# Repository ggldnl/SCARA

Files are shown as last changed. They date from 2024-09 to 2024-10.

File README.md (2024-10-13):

# SCARA

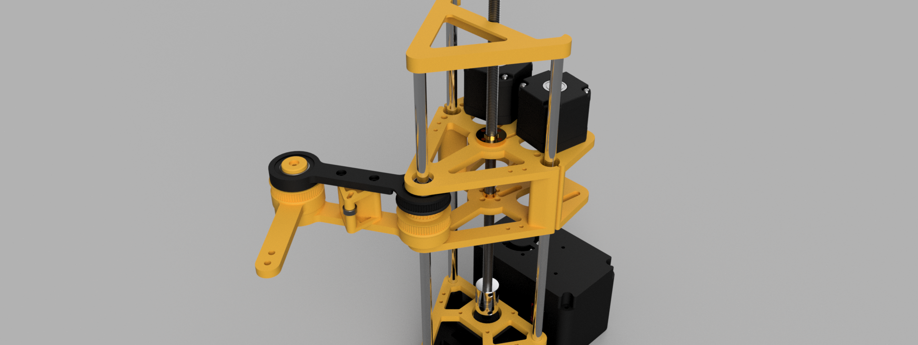
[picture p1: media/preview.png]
Preview


The SCARA (Selective Compliance Assembly Robot Arm) is a type of robotic arm designed for tasks requiring high precision and speed, like assembly and pick-and-place operations. Its configuration allows for rigid vertical movement while maintaining flexibility in the horizontal plane. 

This repository contains the design files, source code, and documentation for my SCARA robotic arm (forgive the redundancy). The arm is mostly 3d printed in order to offer a balance between affordability and functionality.

## Project history and current state

I wanted to build a simple robotic arm and found out the [pyBot](https://jjrobots.com/) project that seemed to have a lot of potential and looked like a good starting point for further development. As I finished assembling the hardware according to the guide, the domain for the website hosting the project expired and was not renewed. At the time of writing this README, the site is still offline, meaning I no longer had access to the original code. The printable files are still available on Thingiverse [here](https://www.thingiverse.com/thing:4579405), and the Hackaday page is still accessible [here](https://hackaday.io/project/175419-pybot-scara-robotic-arm-3d-printed-python).

Considering the situation, I decided to build my own robotic arm taking inspiration from this project. I redesigned everything from scratch in Fusion 360 to have precise control over the robot arm's parameters and to have accurate measurements for the inverse kinematics. The improvements with respect to the previous version include:

- tensioners for joint 2 and 3.
- endstops for each motor, essential for calibration and to recover from missed steps.
- heat set inserts to avoid screwing directly into the plastic.
- simplified assembly for joints 2 and 3.
- properly designed transmission gears.
- improved `z_base` support to joints 2 and 3, now consisting of two pieces.
- control box for better organization, with optional fan to keep the stepper driver cool.
- universal tool mounting point (not limited to the previous servo motor insert).
- clean code with no external dependency (I wrote all the libraries I used), modular and easy to read and understand .

Some renders of the arm in Fusion 360:

<table>
  <tr>
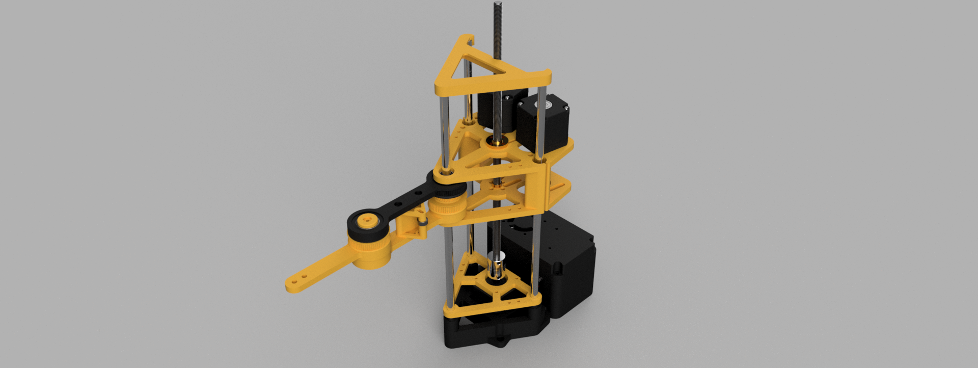
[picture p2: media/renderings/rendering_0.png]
Rendering 0
    <td></td>
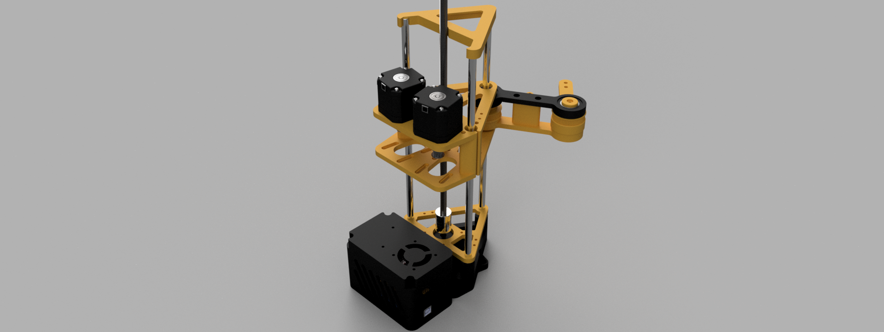
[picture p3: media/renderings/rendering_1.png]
Rendering 1
    <td></td>
  </tr>
  <tr>
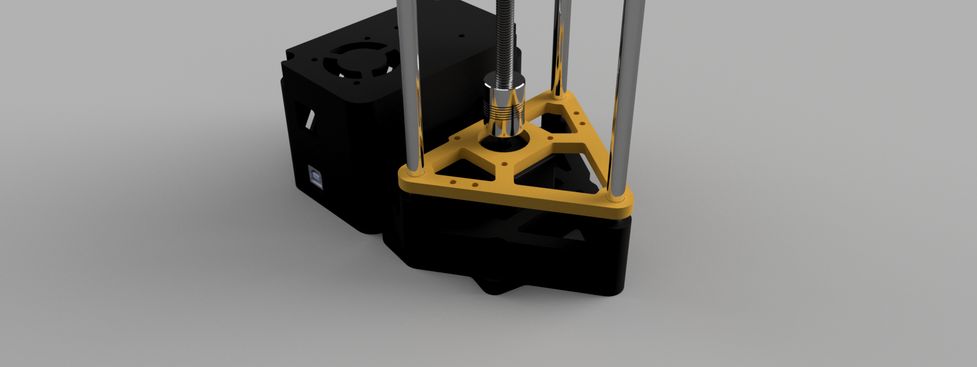
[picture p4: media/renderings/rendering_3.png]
Rendering 2
    <td></td>
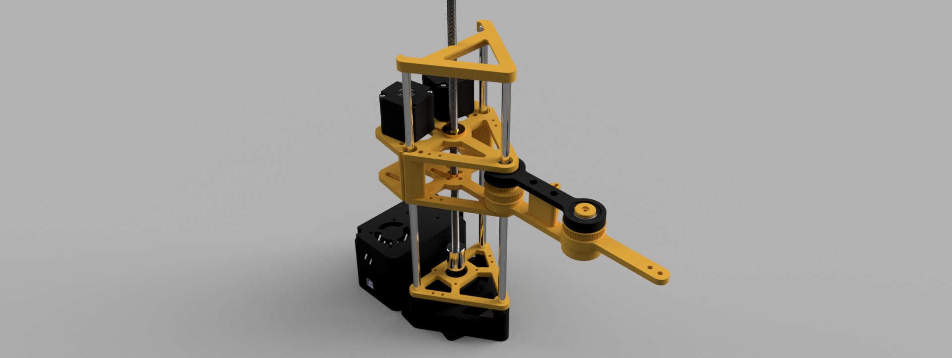
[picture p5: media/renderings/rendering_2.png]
Rendering 3
    <td></td>
  </tr>
  <tr>
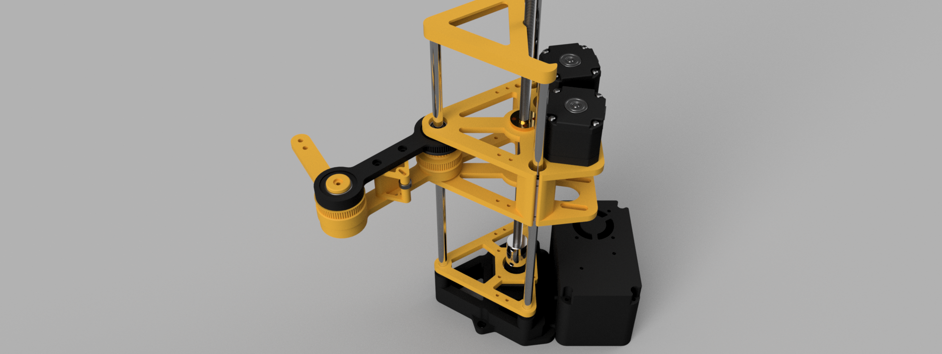
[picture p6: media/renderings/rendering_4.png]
Rendering 4
    <td></td>
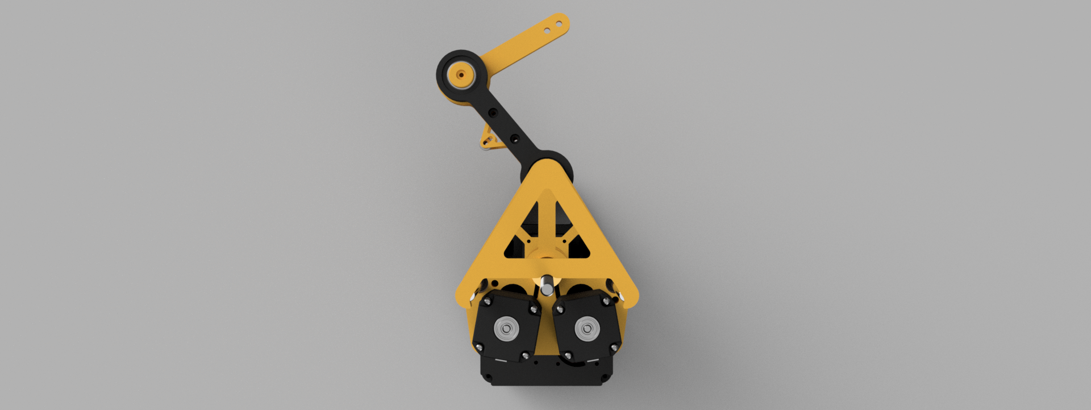
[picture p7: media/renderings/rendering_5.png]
Rendering 5
    <td></td>
  </tr>
</table>

The original project used a DEVIA board, which is an Arduino Zero with built-in sockets for three A4988 stepper motor drivers and onboard drivers for four servos. I opted for an Arduino Uno paired with a CNC shield because it is more accessible, easy to find, and I happened to have both lying around. This setup provides four sockets for stepper drivers and three pins that can be used for the endstops or the end-effector. I also added a 12V mini fan (used for 3d printers) to cool the stepper drivers but this is totally optional. 

## Examples

Homing (https://www.youtube.com/watch?v=YOUTUBE_VIDEO_ID_HERE)

Morning routine (https://www.youtube.com/watch?v=YOUTUBE_VIDEO_ID_HERE)

Pen plotter (https://www.youtube.com/watch?v=YOUTUBE_VIDEO_ID_HERE)

Following a simple straight line (https://www.youtube.com/watch?v=YOUTUBE_VIDEO_ID_HERE)

## 3D printing

You can find all the parts to print in the [hardware/printed_parts](/hardware/printed_parts) folder. Alternatively, you can get them on the platforms below: 

<p align="center">
  <a href="https://makerworld.com/en/models/572256#profileId-492414">
    Open on Makerworld
  </a>
</p>

<p align="center">
  <a href="https://www.thingiverse.com/thing:6743905">
    Open on Thingiverse
  </a>
</p>

<p align="center">
  <a href="https://www.printables.com/en">
    Open on Printables
  </a>
</p>

## Assembly instructions

Check out [here](/hardware/BOM.md) for the Bill of Materials and some notes on what you will need. [Here](/hardware/ASSEMBLY.md) you can find the pdf version of the assembly instructions (that also contains a section on the electronics).

Use [this QR code](https://instructions.online/?id=12092-scara) if you want to follow the instructions on another device:

<p align="center">
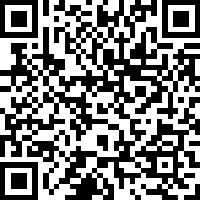
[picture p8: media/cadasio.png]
  
</p>

<!--
<p align="center">
  <a href="https://instructions.online/?id=12092-scara">
    <img src="https://gist.githubusercontent.com/ggldnl/0cb170e629d8188959e9c26c36bc32bd/raw/button_assembly-instructions_fixed_w300_h50.png" alt="Assembly instructions"/>
  </a>
</p>
-->

<!--
## Electronics

<p align="center">
  <img src="media/electronics_stepper_motors.png"/>
</p>

Note:
- Sometimes the cables can have a different color order at the extrema; you should match the connections in this picture;
- Use 3 jumpers for each stepper driver to set the microstepping to 16 (this is what is currently in the config)
  or change the `MICROSTEPPING` value in the config;

<p align="center">
    <img src="media/electronics_limit_switches.png"/>
</p>

After assembling everything and putting together the electronics: download the project > open `software/SCARA/SCARA.ino` from the arduino IDE > compile and upload to the arduino.

-->

## Brief software overview

Summary of the content of each file:

- `vector.hpp`: variable-length vector template class;
- `matrix.hpp`: matrix template class; each matrix has fixed size (not resizable) and exposes methods to compute the determinant, transpose, inverse and even the pseudoinverse along with the classic utility methods   (e.g. indexing, multiplication by matrix/vector etc.);
- `structs.hpp`: structures used to make the code more readable and compact (Point, IKSolution, Steps);
- `button.hpp`: code to handle button events (button pressed and released);
- `logger.hpp`: logger to print formatted strings filtering by logging level (info, warn, error, debug);
- `stepper.hpp`: code to control a stepper motor and make it cover a distance following a trapezoidal/triangular/linear speed profile (everything is expressed in steps, steps/s, steps/s^2);
- `config.hpp`: config file with kinematic structure and velocity/acceleration related constants; You can edit this to adapt the code to your needs;
- `kinematics.hpp`: everything related to this particular robot's kinematics (direct and inverse kinematics, joint velocities computation, ...);
- `SCARA.ino`: main sketch exposing methods to follow a specified trajectory and reach a cartesian point or a joint configuration;

We can use:
- `reachJoint(IKSolution, ...)` to reach a joint configuration with a trapezoidal speed profile;
- `reachCartesian(Point, ...)` to reach a cartesian point with a trapezoidal speed profile;
- `moveStraightLine(Point, Point, ...)` to move between two cartesian points in a straight line interpolating on intermediate positions; we use a linear speed profile between each pair of intermediate points;
- `moveArc(Point, Point, ...)` to move between two cartesian points on an arc interpolating on intermediate positions; we use a linear speed profile between each pair of intermediate points;
- `executeTrajectory(Vector<Point>, ...)` to follow geometric paths; we use the `moveArc(Point, Point, ...)` method between each pair of points; 

<!--
A trajectory is a geometric path + a timing law. In our case things are much simpler and a trajectory is assumed to be a list of points to be reached one after another with a certain velocity (in steps/s). Even if the code to compute joint velocities and thus realize a particular end effector velocity is partially there, I'm not using it (yet?). 

To define your trajectory, replace the section in `SCARA.ino` where the points are added to the trajectory vector. The points in the following example describe a circular trajectory with radius 0.05, center (0.12, 0) and z=0.05 meters:

```cpp
  // Circle (10 points) with radius 0.05  and center (0.12, 0) [meters]
  trajectory.pushBack(Point(0.17, 0.00, 0.05));
  trajectory.pushBack(Point(0.16, 0.03, 0.05));
  trajectory.pushBack(Point(0.14, 0.05, 0.05));
  trajectory.pushBack(Point(0.10, 0.05, 0.05));
  trajectory.pushBack(Point(0.08, 0.03, 0.05));
  trajectory.pushBack(Point(0.07, 0.00, 0.05));
  trajectory.pushBack(Point(0.08, -0.03, 0.05));
  trajectory.pushBack(Point(0.10, -0.05, 0.05));
  trajectory.pushBack(Point(0.14, -0.05, 0.05));
  trajectory.pushBack(Point(0.16, -0.03, 0.05));
```

Calling `executeTrajectory(trajectory)` after this will make the robot execute the trajectory (if feasible i.e. all points are within the reachable workspace and the velocities and acceleration are well conditioned). By default the velocities and acceleration used are the ones defined in the `config.cpp` file but can bypassed using the `executeTrajectory` method's parameters.

-->

## TODO

- [x] Add more renderings
- [ ] Add assembly pdf instructions
- [ ] Update Cadasio instructions
- [x] Add schematic diagram
- [x] Forget AccelStepper/MobaTools and write your own library to simultaneously control multiple steppers
- [x] Add forearm calibration endstop
- [x] Complete the BOM with the list of M3 screws needed
- [ ] Update STLs

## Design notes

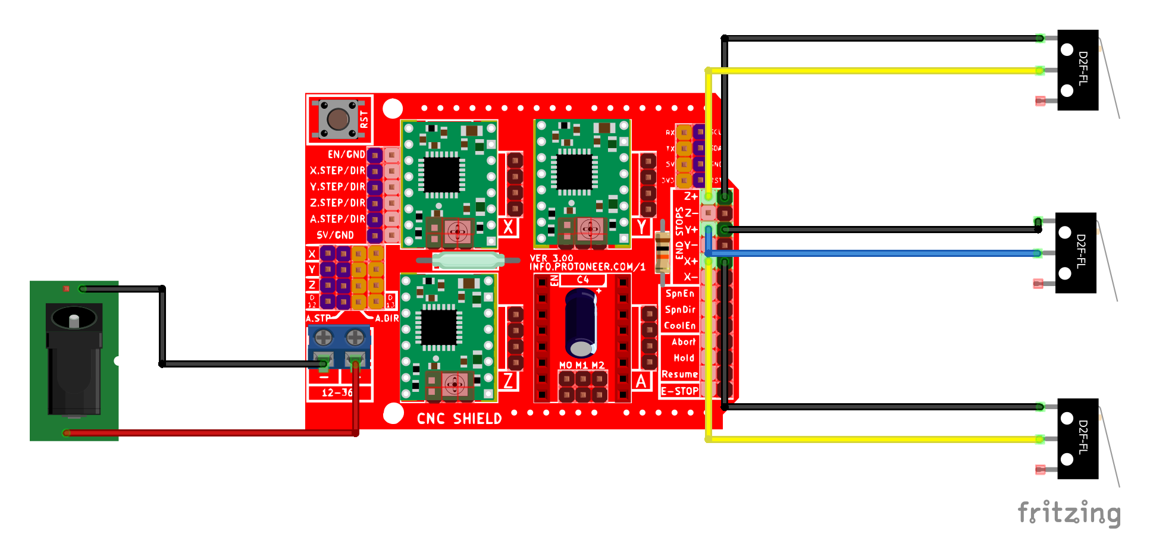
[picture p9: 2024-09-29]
media/electronics_limit_switches.png

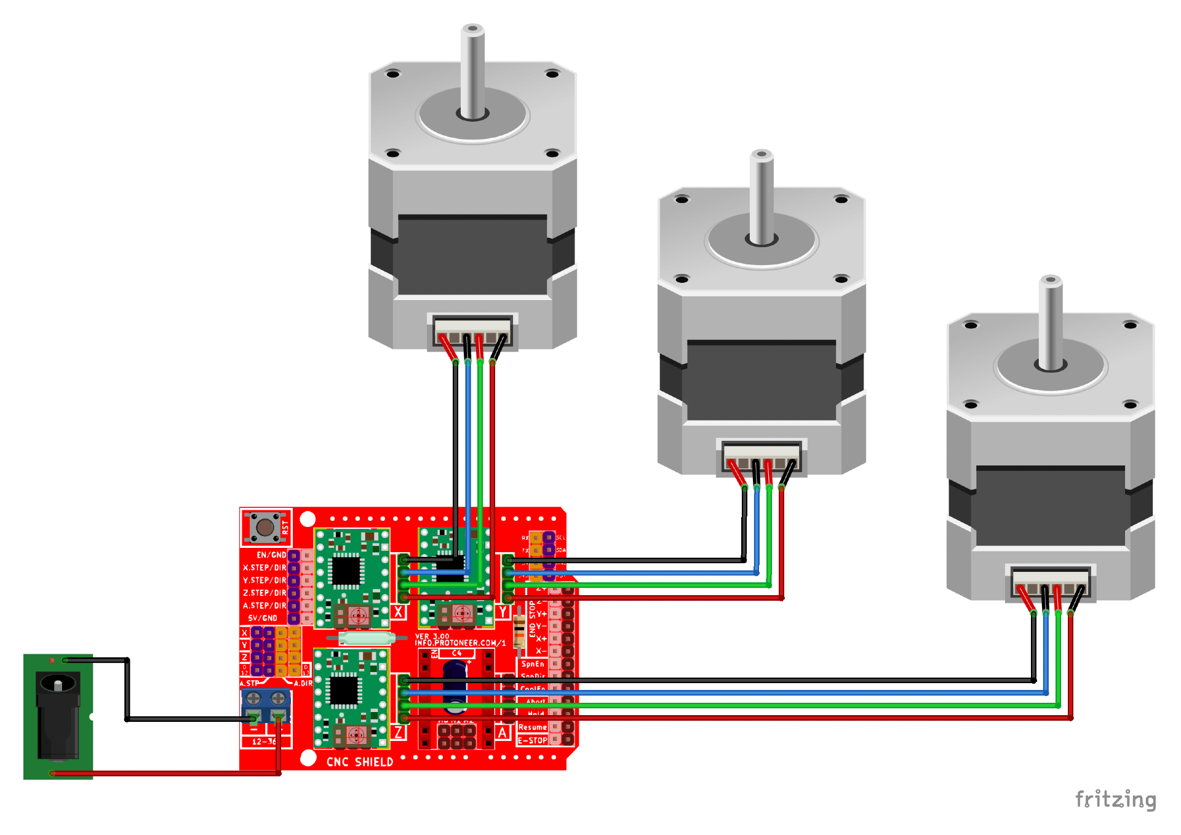
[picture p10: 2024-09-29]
media/electronics_stepper_motors.png

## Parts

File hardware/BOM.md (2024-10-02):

# Bill of Materials (BOM)

| Component | Quantity | Description | Cost (per unit) |
|---|---|---|---|
| NEMA17 stepper motor  | 3 | 1.8° step angle, 12V, 1.5A | € 8.88 |
| Arduino Uno | 1 | | €22.99 |
| CNC shield | 1 | Arduino Uno shield for CNCs | €16.79 |
| Stepper motor driver  | 3 | Stepper drivers based on A4988 | € 1.79 |
| Timing belt | 3 | GT2, 6mm width, 280mm long | € 1.92 |
| Lead screw | 1 | 8mm diameter, 300mm length, with POM nut | € 5.50 |
| Aluminum rods | 3 | 8mm diameter, 300mm length | € 9.99 |
| Pulley | 3 | GT2 for 6mm belt, 16 teeth, 5mm bore | € 1.36 |
| Coupler | 1 | 5mm to 8mm coupler | € 1.60 |
| LM8LUU linear bearing | 3 | Linear bearing, 8mm x 15mm x 45mm | € 2.40 |
| 6002-2RS | 3 | Ball bearing, 15mm x 32mm x 9mm | € 1.42 |
| M3 hex screw kit | 1 | See notes | €11.99 |
| M2 hex screw kit | 1 | See notes | € 7.99 |
| Heat set inserts | 1 | See notes | € 0.06 |
| Locknuts | 1 | See notes | € 0.06 |
| Micro switches | 3 | | € 0.22 |

Total: 150.8 (omitting heat set inserts and locknuts)

## Notes

- Keep in mind that the cost per unit, and consequently the total cost, may vary depending on where you source the parts. For this reason I have not included sourcing links. The listed unit prices reflect now much I paid for each item.
- I did not include zip ties, spiral wraps for the cables and the labels (for which you will also need a labeling machine).
- The aluminum rods I bought are hollow, but this doesn't matter. It's just what was available at the time.
- I added a 12V fan to cool down the stepper drivers but this is totally optional and thus omitted from the BOM. The fan was too loud so I also added a step down converter to decrease the voltage, also optional. If you don't have a step down laying around you can also:
    1. use the fan connecting it directly to the power jack if it's 12V;
    2. use a variable resistor to create a voltage divider and lower its input voltage; this is kind of sketchy and the resistor can get very hot, not recommended;
    3. use a 5V fan and connect it to the 5V and GND pins of the CNC shield;
    
    I provided 3 versions of the control box lid to accomodate each case.
- Number of locknuts used (only where vibrations would unscrew a regular nut): 8
- Number of heat set inserts used: 24
- Complete list of M2 screws and nuts used: 6x M2x16 screw + 6x M2 nuts to keep the micro switches in place 
- Complete list of M3 screws and nuts used:
        2x M3x35
        3x M3x10 (control box lid)
        2x M3x10 (mount arduino to control box)
        2x M3x10 (join control box to base)
        5x M3x10 (forearm)
        10x M3x8 (two z_base and lead screw nut assembly)
        6x M3x16 (limit switches) 
        8x M3 locknuts (limit switches and bottom of the forearm)
        optional - 4x M3x18 (mount fan)
        optional - 2x M3x16 (mount step down voltage regulator)

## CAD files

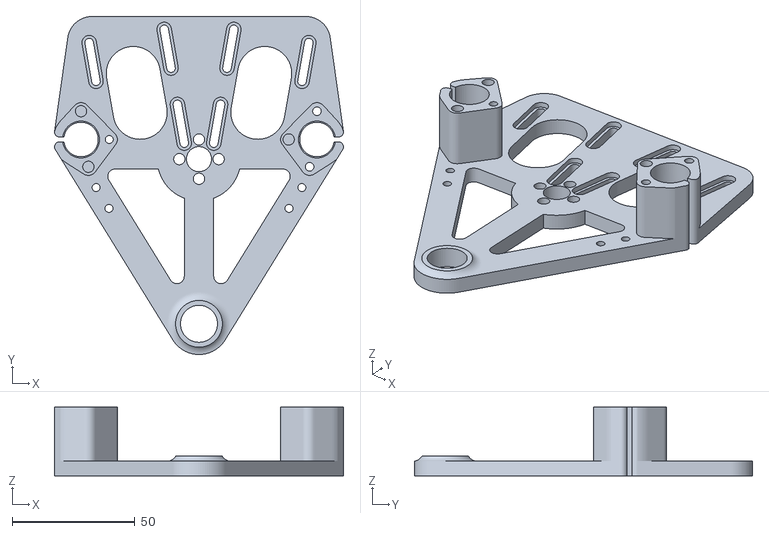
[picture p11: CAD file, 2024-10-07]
hardware/printed_parts/z_base.stl
117.6 x 137.5 x 28.0

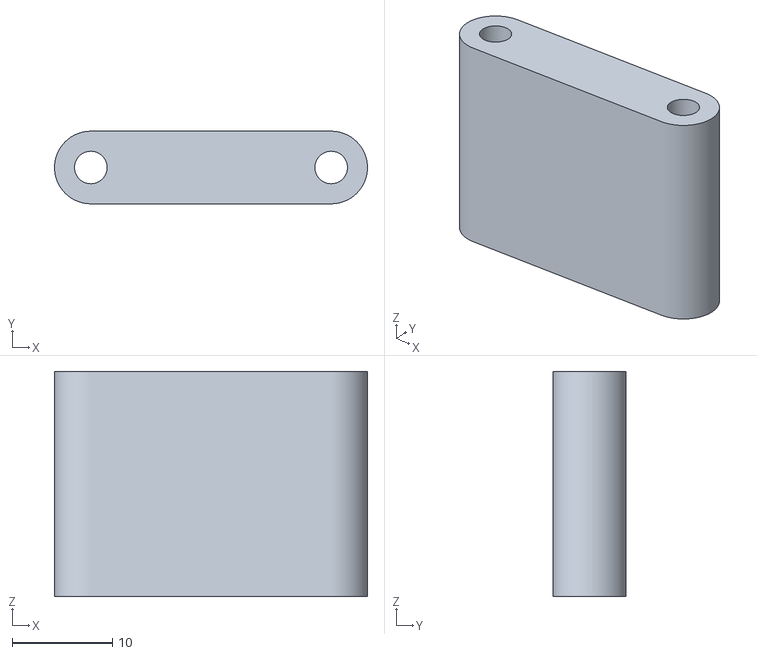
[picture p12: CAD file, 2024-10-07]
hardware/printed_parts/tensioner_bridge.stl
31.2 x 7.25 x 22.5

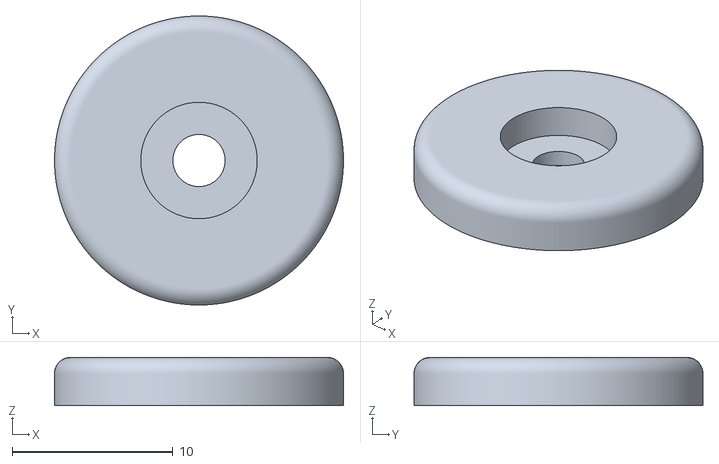
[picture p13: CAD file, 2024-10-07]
hardware/printed_parts/cap.stl
18.0 x 18.0 x 3.00

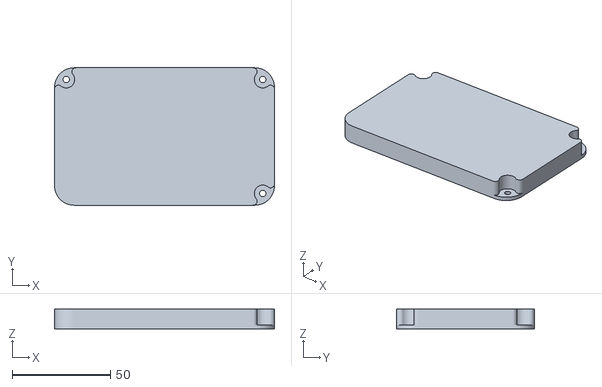
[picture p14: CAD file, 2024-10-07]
hardware/printed_parts/lid.stl
112.0 x 70.0 x 10.0

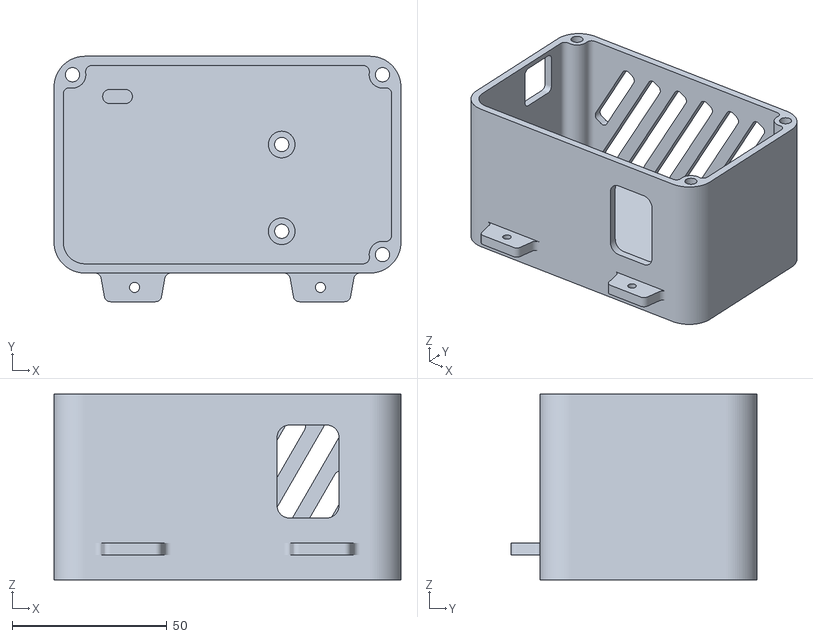
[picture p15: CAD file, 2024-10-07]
hardware/printed_parts/control_box.stl
112.0 x 79.2 x 60.0

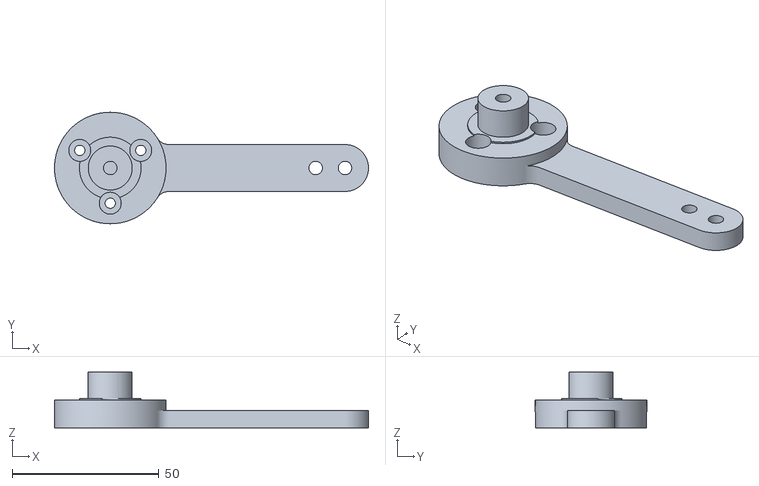
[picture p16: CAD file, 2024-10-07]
hardware/printed_parts/forearm.stl
107.0 x 38.0 x 19.0

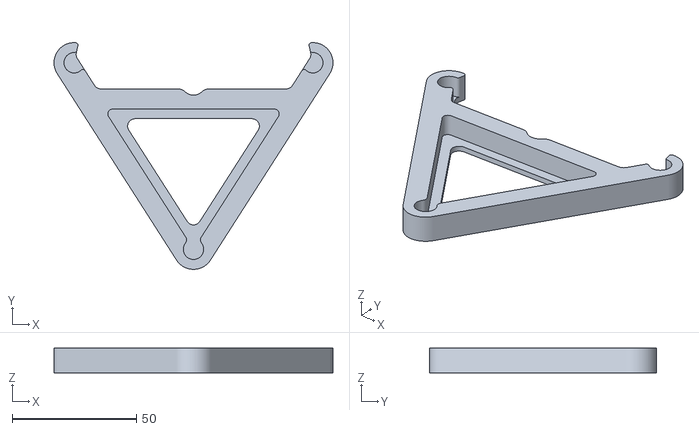
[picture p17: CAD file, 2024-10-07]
hardware/printed_parts/top_triangle.stl
112.2 x 91.2 x 10.0

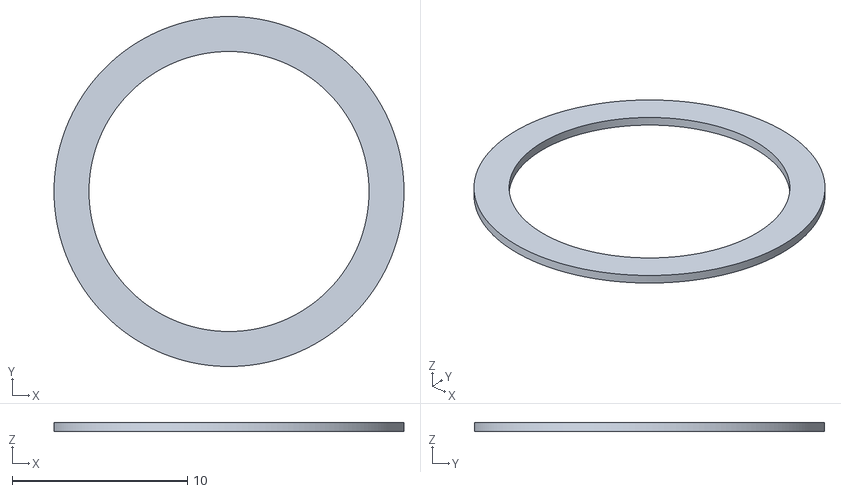
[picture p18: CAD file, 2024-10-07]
hardware/printed_parts/spacer_bottom.stl
20.0 x 20.0 x 0.5

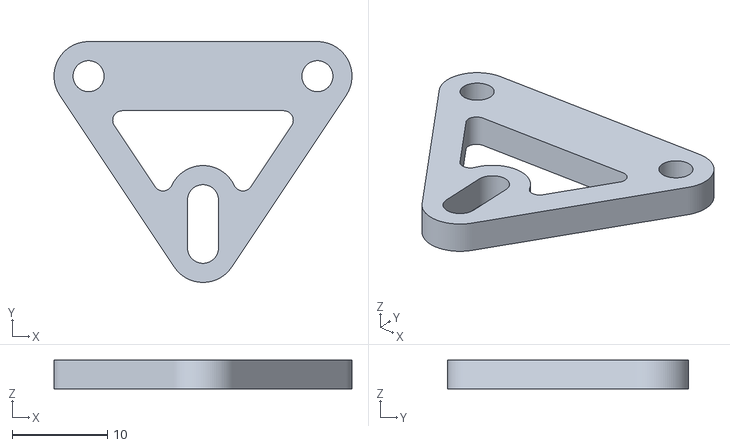
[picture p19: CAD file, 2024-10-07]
hardware/printed_parts/tensioner.stl
31.2 x 25.2 x 3.00

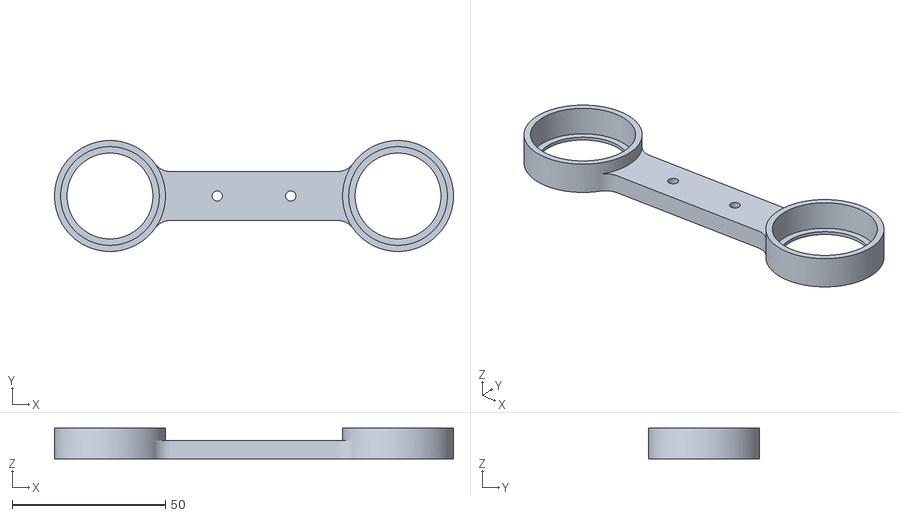
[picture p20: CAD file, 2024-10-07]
hardware/printed_parts/arm_bottom.stl
130.2 x 36.2 x 10.0

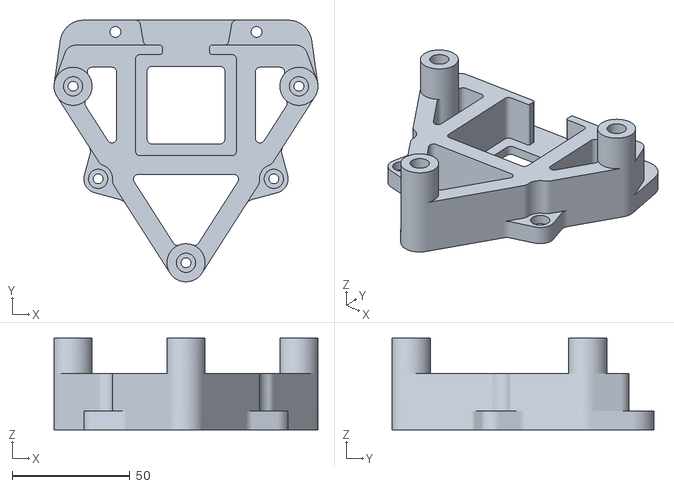
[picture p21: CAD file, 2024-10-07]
hardware/printed_parts/base.stl
112.2 x 111.2 x 39.0

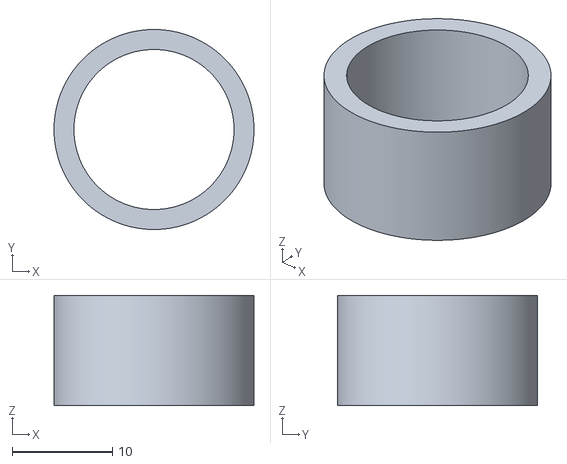
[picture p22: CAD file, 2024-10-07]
hardware/printed_parts/spacer_top.stl
20.0 x 20.0 x 11.0

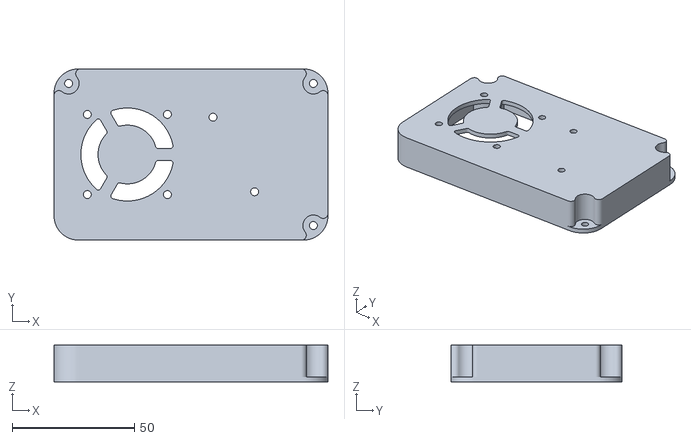
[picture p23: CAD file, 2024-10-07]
hardware/printed_parts/lid_fan_step_down.stl
112.0 x 70.0 x 15.0

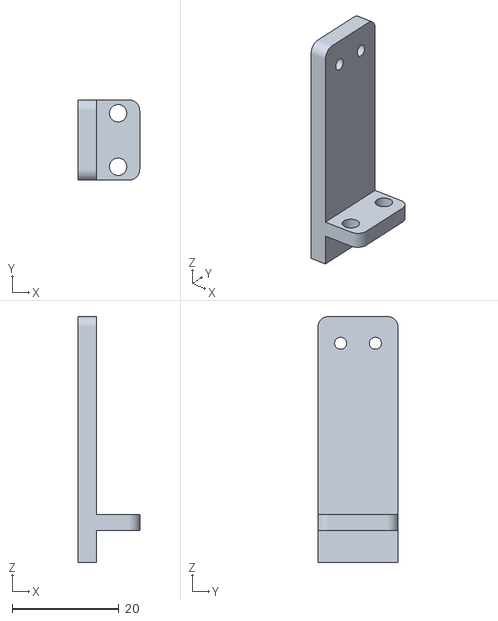
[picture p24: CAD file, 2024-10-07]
hardware/printed_parts/z_endstop.stl
11.5 x 15.0 x 46.0

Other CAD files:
hardware/printed_parts/bottom_triangle.stl
hardware/printed_parts/lid_fan.stl
hardware/printed_parts/arm_top.stl
hardware/printed_parts/xy_endstop.stl
hardware/printed_parts/forearm_reduction.stl
hardware/printed_parts/tensioner_spacer_bottom.stl
hardware/printed_parts/tensioner_spacer_top.stl
hardware/printed_parts/z_base_arm_offset.stl

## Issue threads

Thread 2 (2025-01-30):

The inverse kinematics solution doesn't seem to work

mikhailshevtsov, 2025-01-30:

ggldnl, 2025-01-30:
Can you provide more on the issue?

ggldnl, 2025-01-30:
I already accounted for the fact that link 2 and link 3 are not independent in the code, have you tried it?
The dependence is purely mechanical, due to the motors positioning and transmissions. If you just consider the kinematic model there is no dependence. This is the reason why I momentarily stopped developing the arm, the code is ready and scalable but I'm planning to change almost everything hardware-wise.

Since the two links should be independent the coupling does not show up in the kinematic formulas (in `kinematics.hpp`), but in the main file (`SCARA.ino`, specifically at lines 344-347), when converting from joint values to steps, you can see the offset is added.

Closed 2025-01-31.

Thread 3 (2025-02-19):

SCARA.ino line 347

mikhailshevtsov, 2025-02-19:
Can you explain why we need to adjust third joint by a factor of 2? How to calculate that factor?

ggldnl, 2025-02-19:
It was an empirical finding. After a lot of trials I found that that was pretty much the right value to account for the displacement introduced by the structure of the arm but it is for no means mathematically accurate and this was, once again, a reason why I want to redesign it completely. Let me know if you find a better way of doing this but just out of curiosity, hopefully this problem won't be present in the rework

mikhailshevtsov, 2025-02-19:
Thanks for clarification. I'm also trying to find it empirically. 1.85 seems to be the closest so far.

ggldnl, 2025-02-19:
I suggest you not to put a lot of time into it, unless you already built the arm. If you have experience with cad we can get in touch and work together on the new version

Closed 2025-02-21.

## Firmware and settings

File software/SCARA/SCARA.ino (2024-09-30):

#include "config.hpp"
#include "logger.hpp"
#include "button.hpp"
#include "vector.hpp"
#include "stepper.hpp"
#include "structs.hpp"
#include "kinematics.hpp"

// Function declarations
void executeTrajectory(Vector<Point>&, const double = MIN_VELOCITY_STEPS_S, const double = MIN_VELOCITY_STEPS_S, const double = MIN_VELOCITY_STEPS_S);
void moveStraightLine(const Point&, const Point&, const double = MIN_VELOCITY_STEPS_S, const double = MIN_VELOCITY_STEPS_S, const double =  MIN_VELOCITY_STEPS_S, const int = 20);
void moveArc(const Point&, const Point&, const Point&, const double = MIN_VELOCITY_STEPS_S, const double = MIN_VELOCITY_STEPS_S, const double =  MIN_VELOCITY_STEPS_S, const int = 20);
void reachCartesian(const Point&, const double = MIN_VELOCITY_STEPS_S, const double = MAX_VELOCITY_STEPS_S, const double = MIN_VELOCITY_STEPS_S, const double = ACCELERATION);
void reachJoint(const IKSolution&, const double = MIN_VELOCITY_STEPS_S, const double = MAX_VELOCITY_STEPS_S, const double = MIN_VELOCITY_STEPS_S, const double = ACCELERATION);
Steps IKSolution2Steps(const IKSolution&);
void homeAxis(StepperMotor&, Button&, long, double = HOMING_VELOCITY_STEPS_S);
void homeAll();
void moveAll();
void disable();
void enable();

// Define the steppers
StepperMotor stepper1(STEPPER_1_STEP_PIN, STEPPER_1_DIR_PIN);
StepperMotor stepper2(STEPPER_2_STEP_PIN, STEPPER_2_DIR_PIN);
StepperMotor stepper3(STEPPER_3_STEP_PIN, STEPPER_3_DIR_PIN);

// Define the buttons
Button button1(STEPPER_1_LIMIT_SWITCH_PIN);
Button button2(STEPPER_2_LIMIT_SWITCH_PIN);
Button button3(STEPPER_3_LIMIT_SWITCH_PIN);

// Define the trajectory to follow
Vector<Point> trajectory;

void setup() {

  delay(2000);

  // Initialize serial communication
  Serial.begin(115200);

  // Set log level to INFO
  Logger::setLogLevel(Logger::DEBUG);

  // Initialize the limit switch pins
  pinMode(STEPPER_1_LIMIT_SWITCH_PIN, INPUT_PULLUP);
  pinMode(STEPPER_2_LIMIT_SWITCH_PIN, INPUT_PULLUP);
  pinMode(STEPPER_3_LIMIT_SWITCH_PIN, INPUT_PULLUP);
  Logger::info("Set up limit switches.");

  // Enable the board
  pinMode(ENABLE, OUTPUT);
  enable();
  
  // Home axis
  homeAll();
  Logger::info("All axis homed.");

  /* --------------------------- Execute trajectory --------------------------- */

  // Define an straight line
  trajectory.pushBack(Point(0.10, -0.05, 0.05));
  trajectory.pushBack(Point(0.10, -0.04, 0.05));
  trajectory.pushBack(Point(0.10, -0.03, 0.05));
  trajectory.pushBack(Point(0.10, -0.02, 0.05));
  trajectory.pushBack(Point(0.10, -0.01, 0.05));
  trajectory.pushBack(Point(0.10, 0.01, 0.05));
  trajectory.pushBack(Point(0.10, 0.02, 0.05));
  trajectory.pushBack(Point(0.10, 0.03, 0.05));
  trajectory.pushBack(Point(0.10, 0.04, 0.05));
  trajectory.pushBack(Point(0.10, 0.05, 0.05));
  
  // Position above the first point, a little higher
  reachCartesian(Point(trajectory[0].x, trajectory[0].y, trajectory[1].z + 0.01));

  // Wait for a keypress of the first endstop to start the motion
  while (!button1.pressed()) delay(10);

  executeTrajectory(trajectory, MIN_VELOCITY_STEPS_S, 2000, MIN_VELOCITY_STEPS_S); // peak at 2000 steps/s

  delay(2000);
  disable();
}

/* ------------------------------ Trajectories ------------------------------ */

void executeTrajectory(
    Vector<Point>& trajectory, 
    const double initialVelocity,
    const double maxVelocity,
    const double finalVelocity
    ) {

    for (int i = 0; i < trajectory.getSize() - 1; ++i) {

        // Define velocities
        double vi = i == 0 ? initialVelocity : maxVelocity;
        double vf = i == trajectory.getSize() - 2 ? finalVelocity : maxVelocity;

        moveStraightLine(trajectory[i], trajectory[i + 1], vi, maxVelocity, vf);
    }
}

void moveStraightLine(
  const Point& start,
  const Point& end,
  const double initialVelocity, 
  const double maxVelocity,
  const double finalVelocity,
  const int points
) {

  Vector<Point> interpolatedPoints = interpolateLine3D(start, end, points);

  for (int i = 0; i < interpolatedPoints.getSize(); ++i) {

    Point p = interpolatedPoints[i];

    // Compute the inverse kinematics
    IKSolution configuration;
    bool result = inverseKinematics(p, configuration);
    if (!result) {
      Logger::error("Point ({}, {}, {}) is not reachable.", p.x, p.y, p.z);
      return;
    }
    // Logger::debug("Inverse kinematics solution: ({}, {}, {})", configuration.q1, configuration.q2, configuration.q3);

    // Compute the steps it takes to reach the joint configuration
    Steps steps = IKSolution2Steps(configuration);
    // Logger::debug("Going from: ({}, {}, {})", currSteps.s1, currSteps.s2, currSteps.s3);
    // Logger::debug("        to: ({}, {}, {})", steps.s1, steps.s2, steps.s3);

    // Find longest distance to cover
    long distance1 = abs(stepper1.getCurrentPosition() - steps.s1);
    long distance2 = abs(stepper2.getCurrentPosition() - steps.s2);
    long distance3 = abs(stepper3.getCurrentPosition() - steps.s3);

    double maxSteps = abs(max(distance1, max(distance2, distance3)) * 1.0);

    // The motor that needs to move the most steps should move at full velocity and acceleration
    // while the other motor's velocity and acceleration are scaled proportionally to match 
    // the duration of the motion of the first one. We use 1 if the result is zero to prevent
    // divition by 0
    double scaleFactor1 = (distance1 != 0) ? (maxSteps / distance1) : 1.0;
    double scaleFactor2 = (distance2 != 0) ? (maxSteps / distance2) : 1.0;
    double scaleFactor3 = (distance3 != 0) ? (maxSteps / distance3) : 1.0;

    // Define velocities
    double v1i = i == 0 ? initialVelocity : maxVelocity;
    double v2i = i == 0 ? initialVelocity : maxVelocity;
    double v3i = i == 0 ? initialVelocity : maxVelocity;

    double v1f = i == trajectory.getSize() - 1 ? finalVelocity : maxVelocity;
    double v2f = i == trajectory.getSize() - 1 ? finalVelocity : maxVelocity;
    double v3f = i == trajectory.getSize() - 1 ? finalVelocity : maxVelocity;

    // Scale velocities and accelerations
    v1i = v1i / scaleFactor1;
    v2i = v2i / scaleFactor2;
    v3i = v3i / scaleFactor3;

    v1f = v1f / scaleFactor1;
    v2f = v2f / scaleFactor2;
    v3f = v3f / scaleFactor3;

    stepper1.moveToPosition(steps.s1, v1i, v1f);
    stepper2.moveToPosition(steps.s2, v2i, v2f);
    stepper3.moveToPosition(steps.s3, v3i, v3f);
 
    moveAll();
  }
}

void moveArc(
  const Point& start,
  const Point& end,
  const Point& center,
  const double initialVelocity, 
  const double maxVelocity,
  const double finalVelocity,
  const int points
) {

  Vector<Point> arcPoints = interpolateArc3D(start, end, center, points);

  for (int i = 0; i < arcPoints.getSize(); ++i) {

    Point p = arcPoints[i];

    // Compute the inverse kinematics
    IKSolution configuration;
    bool result = inverseKinematics(p, configuration);
    if (!result) {
      Logger::error("Point ({}, {}, {}) is not reachable.", p.x, p.y, p.z);
      return;
    }

    // Compute the steps it takes to reach the joint configuration
    Steps steps = IKSolution2Steps(configuration);

    // Find longest distance to cover
    long distance1 = abs(stepper1.getCurrentPosition() - steps.s1);
    long distance2 = abs(stepper2.getCurrentPosition() - steps.s2);
    long distance3 = abs(stepper3.getCurrentPosition() - steps.s3);

    double maxSteps = abs(max(distance1, max(distance2, distance3)) * 1.0);

    // Scale factors for proportional motion
    double scaleFactor1 = (distance1 != 0) ? (maxSteps / distance1) : 1.0;
    double scaleFactor2 = (distance2 != 0) ? (maxSteps / distance2) : 1.0;
    double scaleFactor3 = (distance3 != 0) ? (maxSteps / distance3) : 1.0;

    // Define velocities
    double v1i = i == 0 ? initialVelocity : maxVelocity;
    double v2i = i == 0 ? initialVelocity : maxVelocity;
    double v3i = i == 0 ? initialVelocity : maxVelocity;

    double v1f = i == arcPoints.getSize() - 1 ? finalVelocity : maxVelocity;
    double v2f = i == arcPoints.getSize() - 1 ? finalVelocity : maxVelocity;
    double v3f = i == arcPoints.getSize() - 1 ? finalVelocity : maxVelocity;

    // Scale velocities
    v1i = v1i / scaleFactor1;
    v2i = v2i / scaleFactor2;
    v3i = v3i / scaleFactor3;

    v1f = v1f / scaleFactor1;
    v2f = v2f / scaleFactor2;
    v3f = v3f / scaleFactor3;

    // Move motors
    stepper1.moveToPosition(steps.s1, v1i, v1f);
    stepper2.moveToPosition(steps.s2, v2i, v2f);
    stepper3.moveToPosition(steps.s3, v3i, v3f);

    moveAll();
  }
}

/* ------------------------------ Single point ------------------------------ */

void reachCartesian(
  const Point& p,
  const double initialVelocity, 
  const double maxVelocity,
  const double finalVelocity, 
  const double acceleration
  ) {
  /**
   * Reach the target cartesian point from the current position using a 
   * trapezoidal speed profile (if possible). 
   */

  Logger::debug("-------------------------------------------------");
  Logger::debug("Point: ({}, {}, {})", p.x, p.y, p.z);

  // If the point is reachable
  IKSolution solution;
  bool result = inverseKinematics(p, solution);

  if (!result) {
    Logger::error("Point ({}, {}, {}) is not reachable.", p.x, p.y, p.z);
    return;
  }
  Logger::debug("Inverse kinematics solution: ({}, {}, {})", solution.q1, solution.q2, solution.q3);

  reachJoint(solution, initialVelocity, maxVelocity, finalVelocity, acceleration);
}

void reachJoint(
    const IKSolution& solution, 
    const double initialVelocity, 
    const double maxVelocity, 
    const double finalVelocity,
    const double acceleration
  ) {
  /**
   * Reach the target joint configuration using a trapezoidal speed profile
   * (if possible).
   */

  Steps steps = IKSolution2Steps(solution);
  Logger::debug("Going from: ({}, {}, {})", stepper1.getCurrentPosition(), stepper2.getCurrentPosition(), stepper3.getCurrentPosition());
  Logger::debug("        to: ({}, {}, {})", steps.s1, steps.s2, steps.s3);

  // Find longest distance to cover
  long distance1 = abs(stepper1.getCurrentPosition() - steps.s1);
  long distance2 = abs(stepper2.getCurrentPosition() - steps.s2);
  long distance3 = abs(stepper3.getCurrentPosition() - steps.s3);

  double maxSteps = abs(max(distance1, max(distance2, distance3)) * 1.0);
  Logger::debug("Using scaling coefficient: {}", maxSteps);

  // The motor that needs to move the most steps should move at full velocity and acceleration
  // while the other motor's velocity and acceleration are scaled proportionally to match 
  // the duration of the motion of the first one
  double scaleFactor1 = (distance1 != 0) ? (maxSteps / distance1) : 1.0;
  double scaleFactor2 = (distance2 != 0) ? (maxSteps / distance2) : 1.0;
  double scaleFactor3 = (distance3 != 0) ? (maxSteps / distance3) : 1.0;

  // Define velocities
  double v1i = initialVelocity / scaleFactor1;
  double v2i = initialVelocity / scaleFactor2;
  double v3i = initialVelocity / scaleFactor3;

  double v1m = maxVelocity / scaleFactor1;
  double v2m = maxVelocity / scaleFactor2;
  double v3m = maxVelocity / scaleFactor3;

  double v1f = finalVelocity / scaleFactor1;
  double v2f = finalVelocity / scaleFactor2;
  double v3f = finalVelocity / scaleFactor3;

  Logger::debug("-------------------------------------------------");

  stepper1.moveToPosition(steps.s1, v1i, v1m, v1f, acceleration);
  stepper2.moveToPosition(steps.s2, v2i, v2m, v2f, acceleration);
  stepper3.moveToPosition(steps.s3, v3i, v3m, v3f, acceleration);
 
  moveAll(); 
}

void moveAll() {
  /**
   * Move all steppers until they reach the target position.
   */
  while (!(stepper1.isAtTarget() && stepper2.isAtTarget() && stepper3.isAtTarget())) {
    stepper1.step();
    stepper2.step();
    stepper3.step();
  }
}

Steps IKSolution2Steps(const IKSolution& solution) {
  /**
   * Convert the inverse kinematics solution to steps for each motor 
   * by applying reduction factors and compensations.
   */

  Steps steps;
  steps.s1 = solution.q1 * JOINT_1_STEPS_PER_M;
  steps.s2 = solution.q2 * JOINT_2_STEPS_PER_RAD;

  // The third joint is a special case since we need to adjust it by a factor
  // to account for the variation produced by the movement of the second joint.
  steps.s3 = solution.q3 * JOINT_3_STEPS_PER_RAD;
  steps.s3 += solution.q2 / 2 * JOINT_3_STEPS_PER_RAD;

  return steps;
}

/* --------------------------------- Homing --------------------------------- */

void homeAxis(
    StepperMotor& stepper, 
    Button& limitSwitch, 
    long homingSteps, 
    double velocity
  ) {
  /**
   * Home the specified axis by moving the motor with constant speed until button fires.
   * The motor stops after #homingSteps anyway. We can't use a tapezoidal speed profile
   * since we don't know in advance how many steps we need to take and thus we cannot
   * decelerate properly. We could gradually accelerate and until we reach the maximum
   * velocity but I prefer to cruise to the limit switch with minimum velocity in order 
   * to move safely to the target.
   */

  stepper.moveToPosition(homingSteps, velocity, velocity, velocity, 0.1);
  while (!stepper.isAtTarget()) {

    if (limitSwitch.pressed()) {
      Logger::debug("Endstop {} reached.", limitSwitch.getPin());
      break;
    }

    // Perform a step with constant velocity
    stepper.step();

    // Little delay to smooth things out
    delayMicroseconds(10);
  }

  // Set the zero
  stepper.setCurrentPosition(0);
}

void homeAll() {
  /**
   * Home all the axis.
   */

  // Move the first axis down for 10000 steps or until the limit switch registers a press
  homeAxis(stepper1, button1, -MAX_HOMING_STEPS);
  Logger::debug("Axis 0 homed.");

  // homeAxis(stepper2, button2);
  Logger::debug("Axis 1 homed.");

  // homeAxis(stepper3, button3);
  Logger::debug("Axis 2 homed.");

  // Reach the idle position with the arm fully stretched and the z axis at 1cm from the endstop
  reachJoint(IKSolution(0.01, 0, 0)); 
}

void enable() {
  digitalWrite(ENABLE, LOW);
  Logger::debug("Steppers enabled.");
}

void disable() {
  digitalWrite(ENABLE, HIGH);
  Logger::debug("Steppers disabled.");
}

/* ---------------------------------- Loop ---------------------------------- */

void loop() {
  // Nothing to do here
}

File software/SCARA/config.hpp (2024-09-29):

#ifndef CONFIG_HPP
#define CONFIG_HPP

// CNC Shield pinout

const byte STEPPER_1_STEP_PIN = 12; // Axis A requires an optional jumper
const byte STEPPER_2_STEP_PIN = 3;
const byte STEPPER_3_STEP_PIN = 2;

const byte STEPPER_1_DIR_PIN = 13;  // Axis A requires an optional jumper
const byte STEPPER_2_DIR_PIN = 6;
const byte STEPPER_3_DIR_PIN = 5;

const byte ENABLE = 8;  // active-low (i.e. LOW turns on the drivers)

// Velocity and acceleration

/*
 * I empirically found that with my combination of steppers and drivers
 * the stepper work best if we use a pulse with a frequency between
 * 400 and 800 microseconds. A shorter frequency results in a higher
 * velocity. The stepper class works with velocity and accelerations 
 * expressed in steps/s and steps/s^2 respectively. This means that 
 * we would have to use a minimum and maximum velocity in the range 
 * of 1250 to 2500 steps/s, according to the following computation:
 *
 * delay = 1000000/velocity
 * 400 = 1000000/x -> x = 2500
 * 800 = 1000000/x -> x = 1250
 * 
 * The above holds for microstepping 1. Switching to microstepping 16
 * allowed for a wider range of velocities and accelerations.
 */

const double MAX_VELOCITY_STEPS_S = 10000.0;
const double MIN_VELOCITY_STEPS_S = 500.0;
const double ACCELERATION = 5000.0;

// Homing and limit switches

const double HOMING_VELOCITY_STEPS_S = 5000.0;
const long MAX_HOMING_STEPS = 1000000;

const byte STEPPER_1_LIMIT_SWITCH_PIN = 9;
const byte STEPPER_2_LIMIT_SWITCH_PIN = 10;
const byte STEPPER_3_LIMIT_SWITCH_PIN = 11;

// Reduction ratios

const int STEPPER_1_MICROSTEPPING = 16;
const int STEPPER_2_MICROSTEPPING = 16;
const int STEPPER_3_MICROSTEPPING = 16;

const float STEPPER_1_STEPS_PER_REVOLUTION = 200.0;
const float STEPPER_2_STEPS_PER_REVOLUTION = 200.0;
const float STEPPER_3_STEPS_PER_REVOLUTION = 200.0;

const float JOINT_1_LEAD = 8.0;                                 // leadscrew pitch, mm
const float JOINT_2_REDUCTION = (72.0 / 16.0);                  // first stage
const float JOINT_3_REDUCTION = (62.0 / 16.0) * (62.0 / 33.0);  // first stage * second stage

const double JOINT_1_STEPS_PER_M = (STEPPER_1_STEPS_PER_REVOLUTION * STEPPER_1_MICROSTEPPING) / (JOINT_1_LEAD / 1000.0);           // steps/m
const double JOINT_2_STEPS_PER_RAD = (STEPPER_2_STEPS_PER_REVOLUTION * STEPPER_2_MICROSTEPPING / (2 * M_PI)) * JOINT_2_REDUCTION;  // steps/rad
const double JOINT_3_STEPS_PER_RAD = (STEPPER_3_STEPS_PER_REVOLUTION * STEPPER_3_MICROSTEPPING / (2 * M_PI)) * JOINT_3_REDUCTION;  // steps/rad

// Link lenghts

const float L1 = 0.094; // Link 2 length in mm
// const float L2 = 0.080; // Link 3 length in mm
const float L2 = 0.094; // Link 3 + pen plotter length

// Joint limits

const float JOINT_1_MIN_LIMIT = 0;
const float JOINT_1_MAX_LIMIT = 0.2;  // 200 mm, 0.2 m

// The second joint angle should be within the [-pi/2, +pi/2] range
const float JOINT_2_MIN_LIMIT = -M_PI / 2;
const float JOINT_2_MAX_LIMIT = M_PI / 2;

// The third joint angle should be within the [-8pi/9, +8pi/9] range
const float JOINT_3_MIN_LIMIT = -(8 * M_PI) / 9;  // -160 deg
const float JOINT_3_MAX_LIMIT = (8 * M_PI) / 9;   // 160 deg

#endif // CONFIG_HPP

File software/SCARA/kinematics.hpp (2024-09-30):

#ifndef KINEMATICS_HPP
#define KINEMATICS_HPP

#include "config.hpp"
#include "vector.hpp"
#include "matrix.hpp"
#include "structs.hpp"

bool isReachable(const Point& p) {
  float distance = sqrt(p.x * p.x + p.y * p.y);
  return distance <= (L1 + L2) && JOINT_1_MIN_LIMIT <= p.z && p.z <= JOINT_1_MAX_LIMIT;
}

bool inverseKinematics(const Point& p, IKSolution& solution) {

  if (!isReachable(p)) {
    // Logger::debug("Distance: {}", sqrt(p.x * p.x + p.y * p.y));
    return false;  // The point is out of reach
  }

  solution.q1 = p.z;
  float c3 = (p.x * p.x + p.y * p.y - L1 * L1 - L2 * L2) / (2 * L1 * L2);
  float s3_p = sqrt(1 - c3 * c3);
  float q3_p = atan2(s3_p, c3);

  float A = L2 * c3 + L1;
  float B_p = L2 * s3_p;
  float q2_p = atan2(p.y, p.x) - atan2(B_p, A);

  solution.q2 = q2_p;
  solution.q3 = q3_p;

  if (solution.q2 < JOINT_2_MIN_LIMIT || solution.q2 > JOINT_2_MAX_LIMIT)
    return false;

  if (solution.q3 < JOINT_3_MIN_LIMIT || solution.q3 > JOINT_3_MAX_LIMIT)
    return false;

  return true;
}

Vector<IKSolution> inverseKinematicsVector(const Vector<Point>& points) {
  Vector<IKSolution> solutions;

  for (size_t i = 0; i < points.getSize(); i++) {
    IKSolution solution;
    if (!inverseKinematics(points[i], solution)) {
      solutions.clear();
      return solutions;
    }
    solutions.pushBack(solution);
  }

  return solutions;
}

Vector<Point> interpolateLine3D(const Point& start, const Point& end, const int points) {

    Vector<Point> interpolatedPoints(points);

    // If the number of steps is less than or equal to 1, return only the start point
    if (points <= 1) {
        interpolatedPoints.pushBack(start);
        return interpolatedPoints;
    }

    for (int i = 0; i <= points; ++i) {
        
        // Interpolation factor t between 0 and 1
        float t = static_cast<float>(i) / points;

        // Compute the interpolated point
        Point point(
            start.x + t * (end.x - start.x),
            start.y + t * (end.y - start.y),
            start.z + t * (end.z - start.z)
        );

        interpolatedPoints.pushBack(point);
    }

    return interpolatedPoints;
}

Vector<Point> interpolateArc3D(const Point& start, const Point& end, const Point& center, const int points) {

    Vector<Point> interpolatedPoints(points);

    // Vector from center to start and center to end
    Point startToCenter = start - center;
    Point endToCenter = end - center;

    // Compute the radius (assumes both points are at the same distance from the center)
    double radius = startToCenter.magnitude();

    // Compute the angle between the start and end vectors using the dot product
    double startAngle = atan2(startToCenter.y, startToCenter.x);
    double endAngle = atan2(endToCenter.y, endToCenter.x);

    // Ensure the arc goes in the correct direction (counterclockwise)
    if (endAngle < startAngle) {
        endAngle += 2 * M_PI;
    }

    // If steps is less than or equal to 1, return only the start point
    if (points <= 1) {
        interpolatedPoints.pushBack(start);
        return interpolatedPoints;
    }

    // Interpolate points along the arc
    for (int i = 0; i <= points; ++i) {

        // Interpolation factor t between 0 and 1
        double t = static_cast<double>(i) / points;

        // Calculate the interpolated angle between start and end
        double angle = startAngle + t * (endAngle - startAngle);

        // Calculate the position on the arc in the local 2D plane
        double x = center.x + radius * cos(angle);
        double y = center.y + radius * sin(angle);

        // Linearly interpolate the z-coordinate between start and end
        double z = start.z + t * (end.z - start.z);

        // Add the new point to the vector
        interpolatedPoints.pushBack(Point(x, y, z));
    }

    return interpolatedPoints;
}


const Matrix<float> getJacobian(const IKSolution& joints) {
  
  Matrix<float> jacobian(3, 3);

  float q2 = joints.q2;
  float q3 = joints.q3;

  jacobian(0, 0) = 0;
  jacobian(0, 1) = -L2 * sin(q2 + q3) - L1 * sin(q2);
  jacobian(0, 2) = -L2 * sin(q2 + q3);

  jacobian(1, 0) = 0;
  jacobian(1, 1) = L2 * cos(q2 + q3) + L1 * cos(q2);
  jacobian(1, 2) = L2 * cos(q2 + q3);

  jacobian(2, 0) = 1;
  jacobian(2, 1) = 0;
  jacobian(2, 2) = 0;

  return jacobian;
}

const Matrix<float> getJacobianInverse(const IKSolution& joints, const float epsilon = 1e-6) {
  
  Matrix<float> jacobianInverse(3, 3);

  float q2 = joints.q2;
  float q3 = joints.q3;

  float denom_1 = L1 * cos(q2 + q3) * sin(q2) - L1 * sin(q2 + q3) * cos(q2);
  float denom_2 = L1 * L2 * cos(q2 + q3) * sin(q2) - L1 * L2 * sin(q2 + q3) * cos(q2);

  if (fabs(denom_1) < epsilon) denom_1 = epsilon;
  if (fabs(denom_2) < epsilon) denom_2 = epsilon;

  jacobianInverse(0, 0) = 0;
  jacobianInverse(0, 1) = 0;
  jacobianInverse(0, 2) = 1;

  jacobianInverse(1, 0) = -cos(q2 + q3) / denom_1;
  jacobianInverse(1, 1) = -sin(q2 + q3) / denom_1;
  jacobianInverse(1, 2) = 0;

  jacobianInverse(2, 0) = (L2 * cos(q2 + q3) + L1 * cos(q2)) / denom_2;
  jacobianInverse(2, 1) = (L2 * sin(q2 + q3) + L1 * sin(q2)) / denom_2;
  jacobianInverse(2, 2) = 0;

  return jacobianInverse;
}

void perturbJointAngles(IKSolution& joints, const float epsilon = 1e-6, const float perturbation = 1e-2) {
    /**
     * Slightly modify the joint angles to move out of a singularity.
     * Apply a small perturbation to one or more joints to "nudge" out of singular configurations.
     */

    float q1 = joints.q1;
    float q2 = joints.q2;
    float q3 = joints.q3;
    
    // Apply a small perturbation to q2 and q3
    joints.q1 = q1;  // Keep q1 the same as we cannot have singularities here
    joints.q2 = (fabs(q2) < epsilon || fabs(q2 - M_PI/2) < epsilon || fabs(q2 + M_PI/2) < epsilon) ? q2 + perturbation : q2;
    joints.q3 = (fabs(q3) < epsilon || fabs(q3 - M_PI/2) < epsilon || fabs(q3 + M_PI/2) < epsilon) ? q3 + perturbation : q3;

}
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

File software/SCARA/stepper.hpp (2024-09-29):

#ifndef STEPPER_MOTOR_HPP
#define STEPPER_MOTOR_HPP


class SpeedProfile {
  public:
    virtual void compute(long totalSteps, double initialVelocity, double finalVelocity, double maxVelocity = 0, double acceleration = 0) = 0;
    virtual double update(long currentStep) = 0;
};

class TrapezoidalSpeedProfile : public SpeedProfile {
  private:
    double maxVelocity;
    double initialVelocity, finalVelocity, acceleration;
    long accelSteps, decelSteps, constSteps, totalSteps;

  public:
    void compute(long _totalSteps, double _initialVelocity, double _finalVelocity, double _maxVelocity = 0, double _acceleration = 0) override {
      totalSteps = _totalSteps;
      initialVelocity = _initialVelocity;
      maxVelocity = _maxVelocity;
      finalVelocity = _finalVelocity;
      acceleration = _acceleration;

      // Calculate accelSteps, decelSteps, etc.
      accelSteps = abs((maxVelocity * maxVelocity - initialVelocity * initialVelocity) / (2 * acceleration));
      decelSteps = abs((maxVelocity * maxVelocity - finalVelocity * finalVelocity) / (2 * acceleration));
      constSteps = totalSteps - (accelSteps + decelSteps);

      // Fallback to triangular profile if necessary
      if (accelSteps + decelSteps > totalSteps) {
          maxVelocity = sqrt(acceleration * totalSteps + 0.5 * (initialVelocity * initialVelocity + finalVelocity * finalVelocity));
          accelSteps = abs((maxVelocity * maxVelocity - initialVelocity * initialVelocity) / (2 * acceleration));
          decelSteps = totalSteps - accelSteps;
          constSteps = 0;
      }
    }

    double update(long currentStep) override {
      // Handle the trapezoidal speed profile update logic
      if (currentStep < accelSteps) {
        return sqrt(initialVelocity * initialVelocity + 2 * acceleration * currentStep);
      } else if (currentStep < totalSteps - decelSteps) {
        return maxVelocity;
      } else {
        return sqrt(finalVelocity * finalVelocity + 2 * acceleration * (totalSteps - currentStep));
      }
    }
};

class LinearSpeedProfile : public SpeedProfile {
  private:
    double initialVelocity, finalVelocity, increment;
    long totalSteps;

  public:
    void compute(long _totalSteps, double _initialVelocity, double _finalVelocity, double _maxVelocity = 0, double _acceleration = 0) override {
      totalSteps = _totalSteps;
      initialVelocity = _initialVelocity;
      finalVelocity = _finalVelocity;

      // Calculate increment for linear velocity change
      increment = (finalVelocity - initialVelocity) / totalSteps;
    }

    double update(long currentStep) override {
      // Linearly interpolate the velocity
      return initialVelocity + currentStep * increment;
    }
};

class StepperMotor {
  private:
    
    // Pins
    uint8_t pulPin, dirPin;
    
    // Position
    long currentPosition, targetPosition;
    long totalSteps, currentStep;
    bool direction;
    
    // Velocity
    unsigned long stepInterval, lastStepTime;
    double currentVelocity;
    
    // Speed profile
    SpeedProfile* speedProfile; // Pointer to current speed profile
    TrapezoidalSpeedProfile trapezoidalProfile;
    LinearSpeedProfile linearProfile;
    
    void initializeMove(long _targetPosition, double _initialVelocity) {
        targetPosition = _targetPosition;
        currentStep = 0;
        
        totalSteps = abs(targetPosition - currentPosition);
        direction = (targetPosition > currentPosition) ? HIGH : LOW;
        digitalWrite(dirPin, direction);
        
        // Set initial delay
        stepInterval = 1e6 / _initialVelocity;
        lastStepTime = micros();
    }

  public:
    // Constructor
    StepperMotor(uint8_t _pulPin, uint8_t _dirPin) : 
        pulPin(_pulPin), dirPin(_dirPin),
        currentPosition(0), targetPosition(0),
        currentVelocity(0),
        totalSteps(0), currentStep(0),
        stepInterval(0), lastStepTime(0), 
        speedProfile(nullptr),
        direction(true) 
    {
        pinMode(pulPin, OUTPUT);
        pinMode(dirPin, OUTPUT);
    }

    // Check if the stepper has reached the target position
    bool isAtTarget() {
        return currentPosition == targetPosition;
    }
    
    // Linear speed profile
    void moveToPosition(long _targetPosition, double _initialVelocity, double _finalVelocity) {
      speedProfile = &linearProfile;
      initializeMove(_targetPosition, _initialVelocity);
      speedProfile->compute(totalSteps, _initialVelocity, _finalVelocity);
    }
    
    // Trapezoidal speed profile
    void moveToPosition(long _targetPosition, double _initialVelocity, double _maxVelocity, double _finalVelocity, double _acceleration) {
      speedProfile = &trapezoidalProfile;
      initializeMove(_targetPosition, _initialVelocity);
      speedProfile->compute(totalSteps, _initialVelocity, _finalVelocity, _maxVelocity, _acceleration);
    }

    // Perform a step and print current velocity
    void step() {
        
        unsigned long currentTime = micros();
        unsigned long elapsedTime = currentTime - lastStepTime;

        if (currentPosition != targetPosition && elapsedTime >= stepInterval) {

            currentPosition += (direction == HIGH) ? 1 : -1;
            currentStep ++;
            
            if (speedProfile) {
                currentVelocity = speedProfile->update(currentStep);
                stepInterval = 1e6 / currentVelocity;
            }

            // Update the last step time
            lastStepTime = currentTime;

            digitalWrite(pulPin, HIGH);
            delayMicroseconds(1);
            digitalWrite(pulPin, LOW);
        }
    }

    // Set current position manually
    void setCurrentPosition(long _currentPosition) {
        currentPosition = _currentPosition;
    }

    // Get current position
    long getCurrentPosition() {
        return currentPosition;
    }

    // Get current velocity
    double getCurrentVelocity() {
        return currentVelocity;
    }
};

#endif // STEPPER_MOTOR_HPP

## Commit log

2024-07-09 Initial version, testing steppers with no library
2024-07-14 Inverse Kinematics | Homing sequence | Clean stepper control
2024-07-14 Fixed bug with reduction factor for joint 1
    [SCARA.ino]
2024-08-02 Added licence and readme, refactored directory structure
    [arm_joint.stl, arm_lower.stl, base.stl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]
2024-08-05 Fixed error with geometry
    [forearm.stl]
2024-09-06 Added incomplete BOM
2024-09-06 Decreased BOM images size
2024-09-06 Removed images from BOM.md, removed images folder, updated BOM - almost done
2024-09-14 Added notebook on inverse kinematics
2024-09-14 Added direct kinematics
2024-09-15 Completely reworked the code
    [SCARA.ino, config.hpp]
2024-09-15 Added limits to inverse kinematics
2024-09-15 Added other versions of the lid
    [control_box_lid.stl, control_box_lid_fan.stl, control_box_lid_fan_step_down.stl]
2024-09-16 Refactored kinematics notebook, added docstrings and comments, added new notebook on trajectory generation
2024-09-16 Cleaned code introducing structs for inverse kinematics solutions, steps and points
2024-09-16 Little adjustments
    [control_box_lid_fan.stl, control_box_lid_fan_step_down.stl]
2024-09-16 Updated BOM
2024-09-16 Updated z_endstop by adding recess for M2 nuts to keep them safe from vibrations
    [z_endstop.stl]
2024-09-18 TODO check velocity (sometimes is expressed as steps/s, sometimes as m/s, it's a mess
2024-09-25 Finetuned parameters & changed test trajectory | Still lot of bugs
    [SCARA.ino, config.hpp]
2024-09-26 Fixed steps bug (switching from int to long and from float to double) and completed homing
    [SCARA.ino, config.hpp]
2024-09-26 Removed some logs (too many) due to runtime errors (?), changed trajectory
    [SCARA.ino]
2024-09-28 Cleaned the code a bit (this exposed some bugs)
    [SCARA.ino, config.hpp, kinematics.hpp]
2024-09-29 Updated StepperMotor class now supports trapezoidal, triangular and linear speed profiles
2024-09-29 Added 3D line interpolation to kinematics.hpp
2024-09-29 Updated velocities
2024-09-29 Added schematic showing how to connect the stepper motors
2024-09-29 Added schematic showing how to connect limit switches
2024-10-02 Updated BOM.md
2024-10-07 Reworked printed parts, need testing
    [arm_bottom.stl, arm_joint.stl, arm_lower.stl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]
